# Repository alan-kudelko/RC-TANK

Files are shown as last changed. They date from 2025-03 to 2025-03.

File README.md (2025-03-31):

# Full-metal RC-TANK in 1:11 Scale
Project of full-metal RC-TANK in 1:11 scale made from 3mm thick steel sheets  
### 1. Requirements:

Tab.1.1 Tank Dimensions

| Dimension | |
|---|---|
| $Length$ | 70 [cm] |
| $Width_{1}$  | 32 [cm] |
| $Width_{2}$  | 42 [cm] |
| $Height$ | 20 [cm] |
| $Ground\ clearance$ | 5 [cm] |

###### $Width_{1}$ - Width of tank without tracks  
###### $Width_{2}$ - Width of tank with tracks  
2. Maximum speed  of at least $V_{Max}=5\frac{km}{h}$  
3. Input battery voltage $U_{In}=12.5V - 35V$  
4. DC Motors voltage $U_{m}=7.4V$  
### 2. Tracks and sprocket wheels

<picture>
 <source media="(prefers-color-scheme: dark)" srcset="Drivetrain/Tank_Tracks.png">
 <source media="(prefers-color-scheme: light)" srcset="Drivetrain/Tank_Tracks.png">
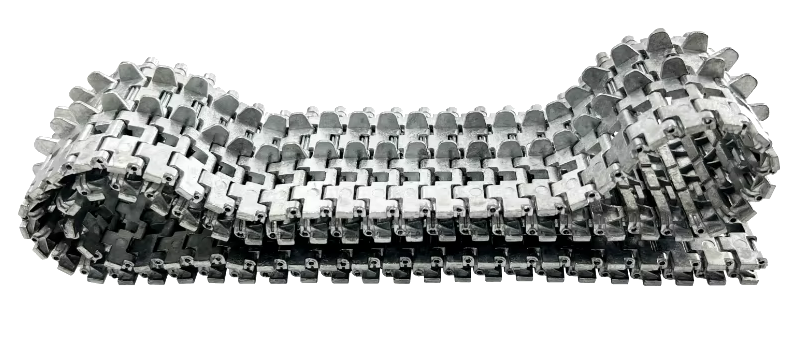
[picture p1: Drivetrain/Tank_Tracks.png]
 
</picture>

<picture>
 <source media="(prefers-color-scheme: dark)" srcset="Drivetrain/Sprocket_Wheel.png">
 <source media="(prefers-color-scheme: light)" srcset="Drivetrain/Sprocket_Wheel.png">
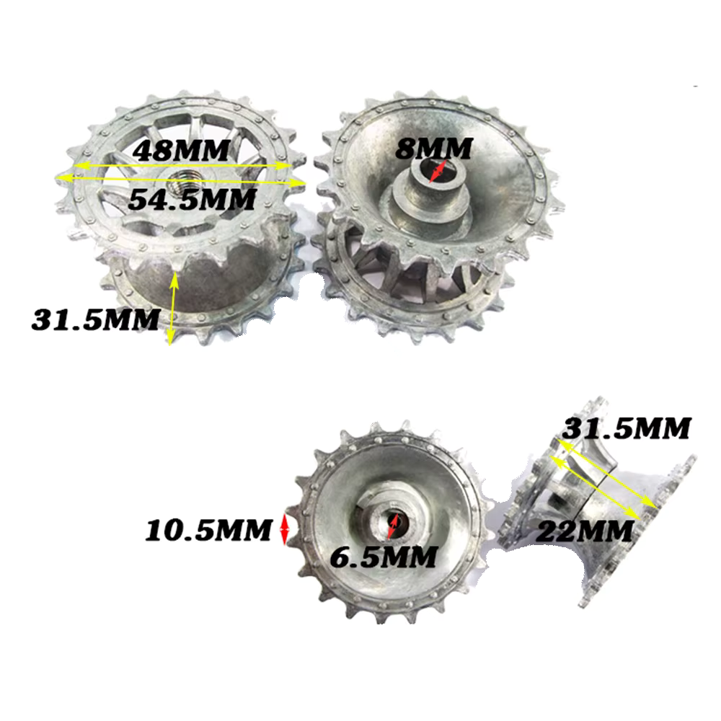
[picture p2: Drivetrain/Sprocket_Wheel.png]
 
</picture>

### 3. DC Motors selection
<picture>
 <source media="(prefers-color-scheme: dark)" srcset="Drivetrain/Injora540_13T_Parameters.png">
 <source media="(prefers-color-scheme: light)" srcset="Drivetrain/Injora540_13T_Parameters.png">
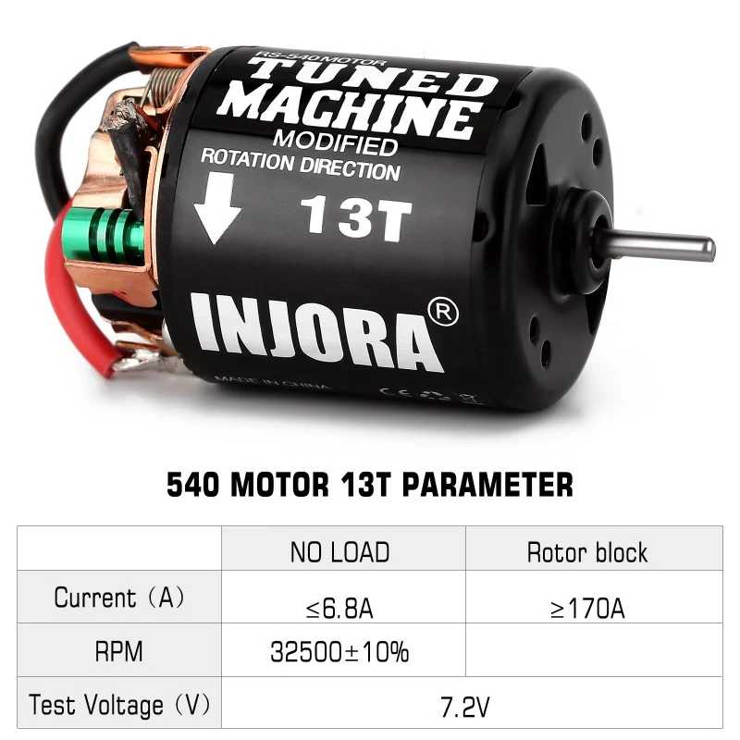
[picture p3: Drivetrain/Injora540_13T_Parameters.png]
 
</picture>

<picture>
 <source media="(prefers-color-scheme: dark)" srcset="Drivetrain/Injora540_Parameters_Comparison.png">
 <source media="(prefers-color-scheme: light)" srcset="Drivetrain/Injora540_Parameters_Comparison.png">
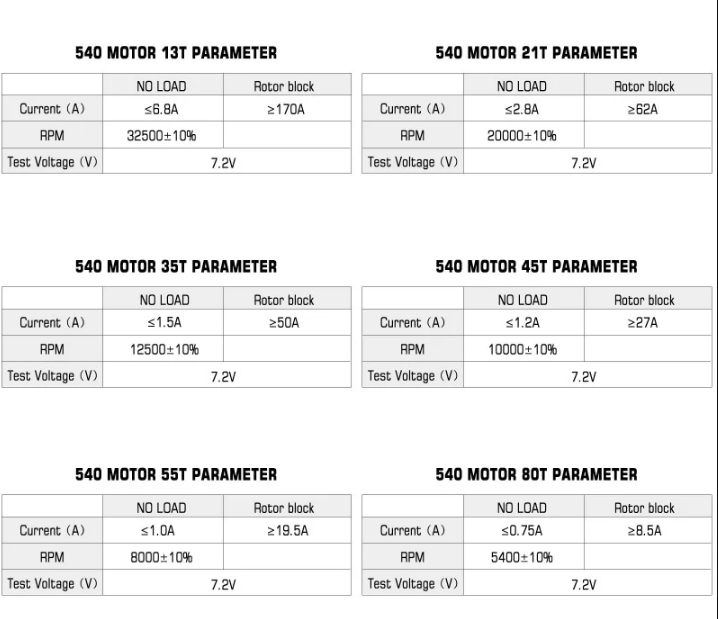
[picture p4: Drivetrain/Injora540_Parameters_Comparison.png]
 
</picture>

According to graphs Injora 540 13T has the highest peak power of around 300W but its RPM is too high for usage in a RC Tank. In order to able to move heavy vehicle we need to use a gearbox.

<picture>
 <source media="(prefers-color-scheme: dark)" srcset="Drivetrain/DC_Motor_Selection.png">
 <source media="(prefers-color-scheme: light)" srcset="Drivetrain/DC_Motor_Selection.png">
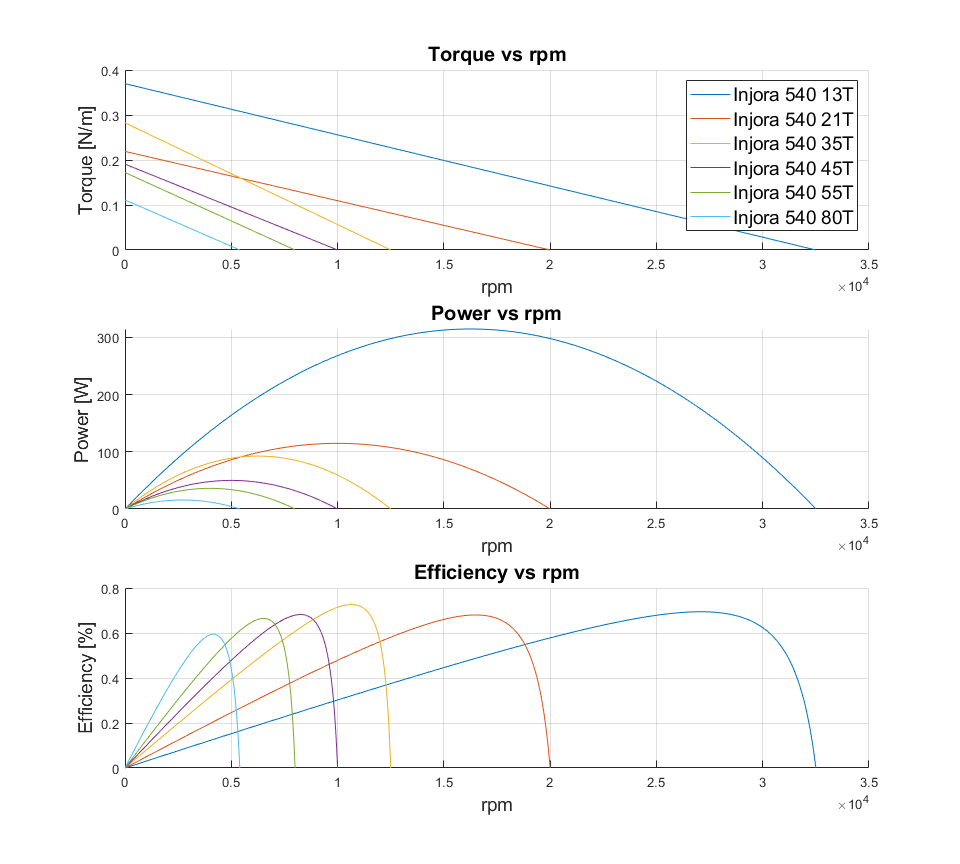
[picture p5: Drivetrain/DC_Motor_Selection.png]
 
</picture>

### 4. Gearbox selection   
<picture>
 <source media="(prefers-color-scheme: dark)" srcset="Drivetrain/DC_Motor_Gearbox_1_50.png">
 <source media="(prefers-color-scheme: light)" srcset="Drivetrain/DC_Motor_Gearbox_1_50.png">
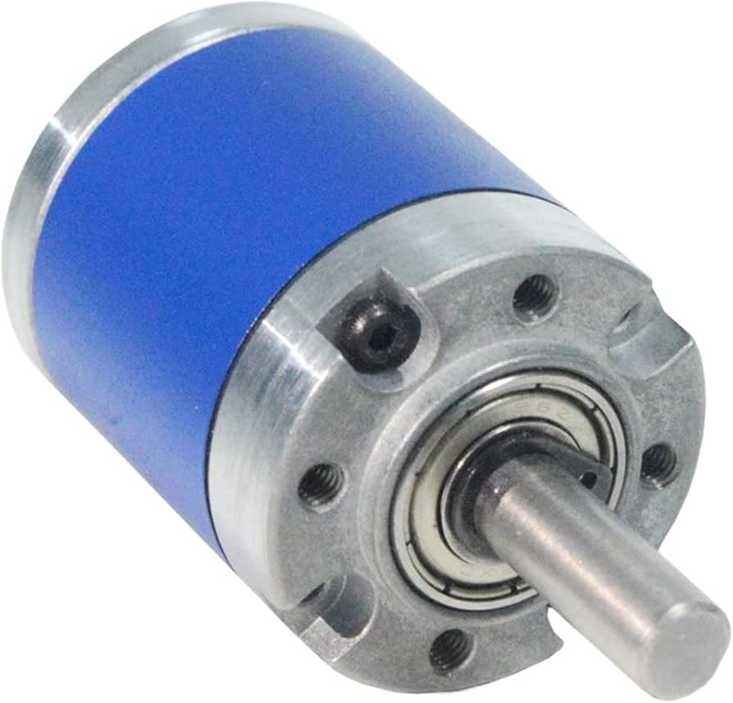
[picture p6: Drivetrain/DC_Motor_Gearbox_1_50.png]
 
</picture>

<picture>
 <source media="(prefers-color-scheme: dark)" srcset="Drivetrain/DC_Motor_Gearbox_dims_1.png">
 <source media="(prefers-color-scheme: light)" srcset="Drivetrain/DC_Motor_Gearbox_dims_1.png">
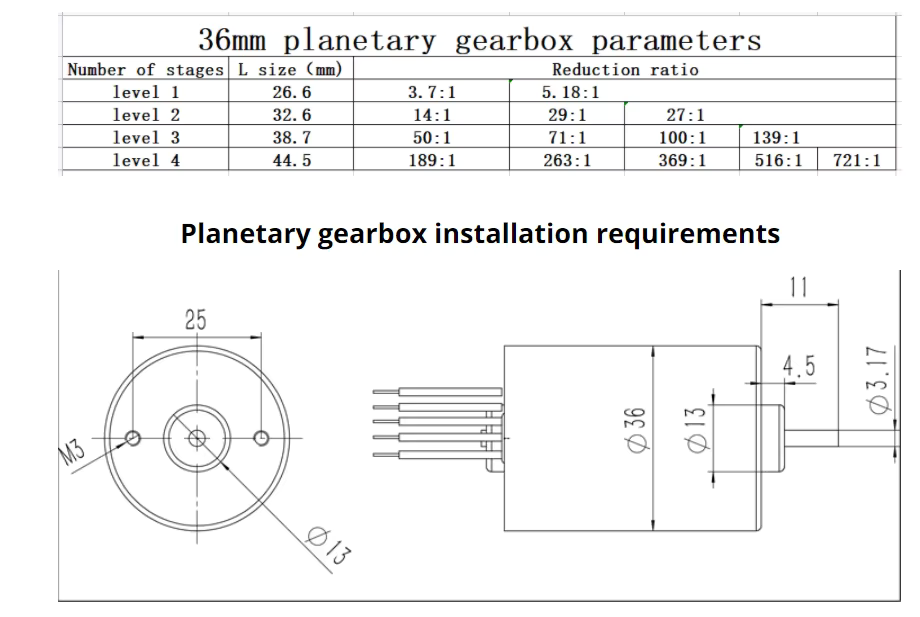
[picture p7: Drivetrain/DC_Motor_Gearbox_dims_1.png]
 
</picture>

<picture>
 <source media="(prefers-color-scheme: dark)" srcset="Drivetrain/DC_Motor_Gearbox_dims_2.png">
 <source media="(prefers-color-scheme: light)" srcset="Drivetrain/DC_Motor_Gearbox_dims_2.png">
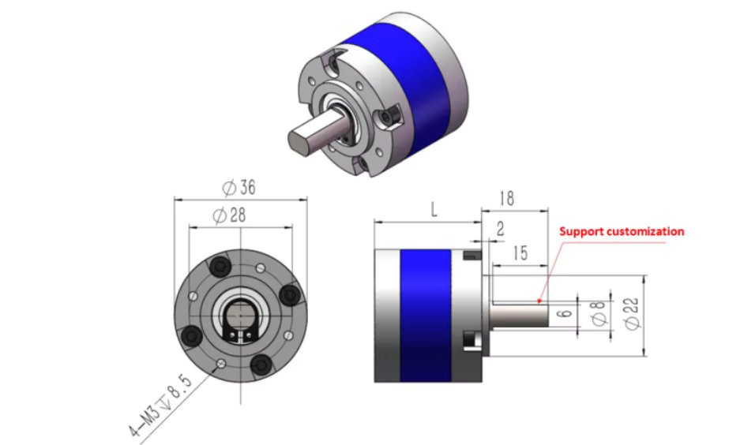
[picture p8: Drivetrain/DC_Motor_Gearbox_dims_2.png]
 
</picture>

<picture>
 <source media="(prefers-color-scheme: dark)" srcset="Drivetrain/DC_Motor_Gearbox_Selection.png">
 <source media="(prefers-color-scheme: light)" srcset="Drivetrain/DC_Motor_Gearbox_Selection.png">
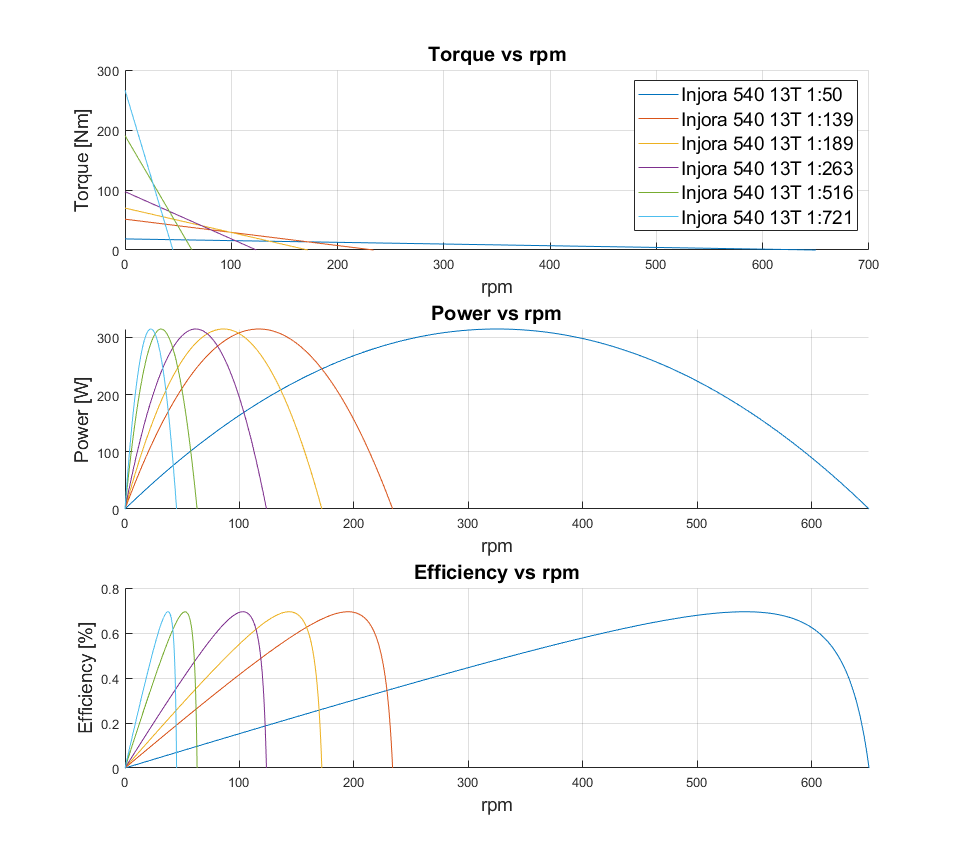
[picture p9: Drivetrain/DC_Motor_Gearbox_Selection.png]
 
</picture>

Speed of the tank has to be at least $V_{Max}=5\frac{km}{h}$

Tab.4.1 Drivetrain parameters

| Drivetrain parameters | |
|---|---|
| Sprocket wheel diameter | D=48 [mm] |
| RPM  | n=32500 [rpm] |
| Gearbox reduction  | r=1:50 |

We can see that the selected DC motor with 1:50 gearbox gives theoretical 650 rpm.

Using a formula 1) we can calculate maximum theoretical speed of a tank.

1) $V_{Max}=\pi\frac{D*rpm}{60}=1.63\frac{m}{s}=5.88\frac{km}{h} $

### 5. Switch mode power supply design
Switch mode power supply should be able to generate all the necessery voltages for use in the tank. That are 7.4V for DC motor, 5V for controll logic, 6V for servomechanisms and 12V for additional devices such as DC fans. Additionally it should feature a wide range of input voltages for instance 12.5V - 35V. On top of that power supply should have shortcircuit protection, undervoltage protection and overtemperature protection. Moreover, in order order to limit inrush current for the circuit I decided to use high-side mosfet as softstart.

Tab.5.1 Voltages and current requirements

| Voltage | Maximum current | Maximum power|
|---|---|---|
| 7.4 [V] | 40 [A] | 296 [W] |
| 12 [V] | 20 [A] | 240 [W] |
| 6 [V] | 20 [A] | 120 [W] |
| 5 [V] | 5 [A]  | 25 [W]  |
| Total | 85 [A] | 681 [W] |

When designing switch mode power supply it is advised to choose the right topology depending on power output. That's why, I have decided to use half-bridge topology for sections 7.4V and 12V and buck topology for sections 5V and 6V.

Tab.5.2 Design requirements for section 7.4V

| Voltage | Maximum power|
|---|---|
| Topology| Half-Bridge |
| Output voltage | 7.4 [V]|
| Output current | 40 [A]|
| Working frequency | 500 [kHz] |
| Coil inductance min. | 16 [uH] |
| Coil core material | T130-52 |
| Coil wire diameter | 2.36 [mm] |
| Switching transistors | IXTH94N20X4 |
| Conduction and switching losses per transistor | 22.5 [W] |
| Total power losses| 45 [W]|
| PWM Controller | TL3843 |
| Mosfet driver | IRS2008 |

Tab.5.3 Design requirements for section 12V

| Voltage | Maximum power|
|---|---|
| Topology| Half-Bridge |
| Output voltage | 12 [V]|
| Output current | 20 [A]|
| Working frequency | 500 [kHz] |
| Coil inductance min. | 16 [uH] |
| Coil core material | T106-26B |
| Coil wire diameter | 1.60 [mm] |
| Switching transistors | STP60NF06 |
| Conduction and switching losses per transistor | 16.6 [W]|
| Total power losses | 33.2 [W]|
| PWM Controller | TL3843 |
| Mosfet driver | IRS2008 |

Tab.5.4 Design requirements for section 6V

| Voltage | Maximum power|
|---|---|
| Topology| Buck |
| Output voltage | 6.0 [V]|
| Output current | 20 [A]|
| Working frequency | 500 [kHz] |
| Coil inductance min. | 16 [uH] |
| Coil core material | T106-26B |
| Coil wire diameter | 1.60 [mm] |
| Switching transistor | STP60NF06 |
| Freewheeling diode| RHRP3060|
| Conduction and switching losses in transistors | 16.6 [W] |
| Conduction losses in freewheeling diode| 14 [W]|
| Total power losses | 30.6 [W]|
| PWM Controller | TL3843 |
| Mosfet driver | IRS20752 |

Tab.5.5 Design requirements for section 5V

| Voltage | Maximum power|
|---|---|
| Topology| Buck |
| Output voltage | 5 [V]|
| Output current | 5 [A]|
| Working frequency | 500 [kHz] |
| Coil inductance min. | 16 [uH] |
| Coil core material | T72-52 |
| Coil wire diameter | 0.80 [mm] |
| Switching transistor | STP60NF06 |
| Freewheeling diode| SB560 |
| Conduction and switching losses in transistors | 2.95 [W] |
| Conduction losses in freewheeling diode| 2.8 [W]|
| Total power losses | 5.75 [W]|
| PWM Controller | TL3843 |
| Mosfet driver | IRS20752 |

Tab.5.6 Design requirements for input section

| Voltage | Maximum power|
|---|---|
| Input voltage | 12.5 - 35 [V]|
| Input current | 85 [A]|
| Softstart transistor | IRF100P218AKMA1 |
| Conduction and switching losses in transistors | 9.25 [W] |

Mosfet power losses were calculated using online calculator https://www.heatsinkcalculator.com/mosfet-power-loss-calculator.html   
Gate charge losses were negligible that is why they are not included

Overall simplified schematic of whole SMPS will look similiar to that:

<picture>
 <source media="(prefers-color-scheme: dark)" srcset="SMPS/SMPS_Simplified.PNG">
 <source media="(prefers-color-scheme: light)" srcset="SMPS/SMPS_Simplified.PNG">
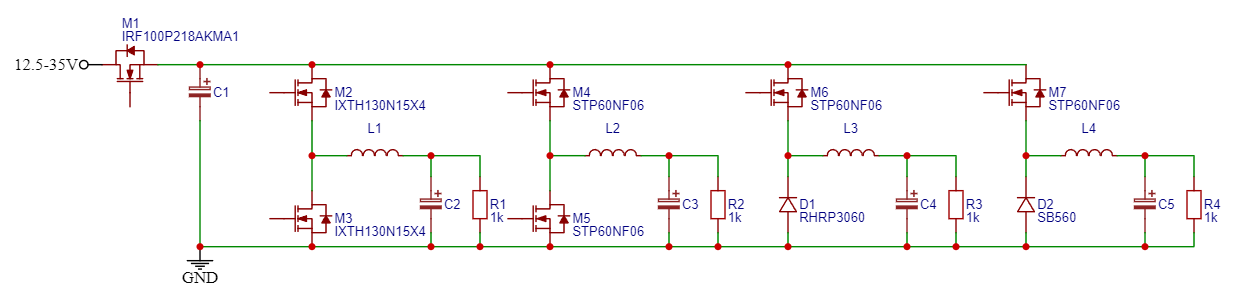
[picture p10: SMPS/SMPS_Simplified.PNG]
 
</picture>

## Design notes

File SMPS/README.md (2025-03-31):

# Switch mode power supply for RC-TANK
Switch mode power supply should be able to generate all the necessery voltages for use in the tank. That are 7.4V for DC motor, 5V for controll logic, 6V for servomechanisms and 12V for additional devices such as DC fans. Additionally it should feature a wide range of input voltages for instance 12.5V - 35V. On top of that power supply should have shortcircuit protection, undervoltage protection and overtemperature protection. Moreover, in order order to limit inrush current for the circuit I decided to use high-side mosfet as softstart.

Tab.1.1 Voltages and current requirements

| Voltage | Maximum current | Maximum power|
|---|---|---|
| 7.4 [V] | 40 [A] | 296 [W] |
| 12 [V] | 20 [A] | 240 [W] |
| 6 [V] | 20 [A] | 120 [W] |
| 5 [V] | 5 [A]  | 25 [W]  |
| Total | 85 [A] | 681 [W] |

When designing switch mode power supply it is advised to choose the right topology depending on power output. That's why, I have decided to use half-bridge topology for sections 7.4V and 12V and buck topology for sections 5V and 6V.

Tab.1.2 Design requirements for section 7.4V

| Voltage | Maximum power|
|---|---|
| Topology| Half-Bridge |
| Output voltage | 7.4 [V]|
| Output current | 40 [A]|
| Working frequency | 500 [kHz] |
| Coil inductance min. | 16 [uH] |
| Coil core material | T130-52 |
| Coil wire diameter | 2.36 [mm] |
| Switching transistors | IXTH94N20X4 |
| Conduction and switching losses per transistor | 22.5 [W] |
| Total power losses| 45 [W]|
| PWM Controller | TL3843 |
| Mosfet driver | IRS2008 |

Tab.1.3 Design requirements for section 12V

| Voltage | Maximum power|
|---|---|
| Topology| Half-Bridge |
| Output voltage | 12 [V]|
| Output current | 20 [A]|
| Working frequency | 500 [kHz] |
| Coil inductance min. | 16 [uH] |
| Coil core material | T106-26B |
| Coil wire diameter | 1.60 [mm] |
| Switching transistors | STP60NF06 |
| Conduction and switching losses per transistor | 16.6 [W]|
| Total power losses | 33.2 [W]|
| PWM Controller | TL3843 |
| Mosfet driver | IRS2008 |

Tab.1.4 Design requirements for section 6V

| Voltage | Maximum power|
|---|---|
| Topology| Buck |
| Output voltage | 6.0 [V]|
| Output current | 20 [A]|
| Working frequency | 500 [kHz] |
| Coil inductance min. | 16 [uH] |
| Coil core material | T106-26B |
| Coil wire diameter | 1.60 [mm] |
| Switching transistor | STP60NF06 |
| Freewheeling diode| RHRP3060|
| Conduction and switching losses in transistors | 16.6 [W] |
| Conduction losses in freewheeling diode| 14 [W]|
| Total power losses | 30.6 [W]|
| PWM Controller | TL3843 |
| Mosfet driver | IRS20752 |

Tab.1.5 Design requirements for section 5V

| Voltage | Maximum power|
|---|---|
| Topology| Buck |
| Output voltage | 5 [V]|
| Output current | 5 [A]|
| Working frequency | 500 [kHz] |
| Coil inductance min. | 16 [uH] |
| Coil core material | T72-52 |
| Coil wire diameter | 0.80 [mm] |
| Switching transistor | STP60NF06 |
| Freewheeling diode| SB560 |
| Conduction and switching losses in transistors | 2.95 [W] |
| Conduction losses in freewheeling diode| 2.8 [W]|
| Total power losses | 5.75 [W]|
| PWM Controller | TL3843 |
| Mosfet driver | IRS20752 |

Tab.1.6 Design requirements for input section

| Voltage | Maximum power|
|---|---|
| Input voltage | 12.5 - 35 [V]|
| Input current | 85 [A]|
| Softstart transistor | IRF100P218AKMA1 |
| Conduction and switching losses in transistors | 9.25 [W] |

Mosfet power losses were calculated using online calculator https://www.heatsinkcalculator.com/mosfet-power-loss-calculator.html   
Gate charge losses were negligible that is why they are not included

Overall simplified schematic of whole SMPS will look similiar to that:

<picture>
 <source media="(prefers-color-scheme: dark)" srcset="SMPS_Simplified.PNG">
 <source media="(prefers-color-scheme: light)" srcset="SMPS_Simplified.PNG">
 YOUR-ALT-TEXT
</picture>

Current project of PCB board is a proof of concept which will allow to test the following:
1. Input MOSFET with RC circuit softstart   
2. TL3843 - PWM Controller   
3. IRS20752 - High side MOSFET DRIVER with bootstraping   
4. Output voltages   
5. Step-up conveter for gate of input MOSFET

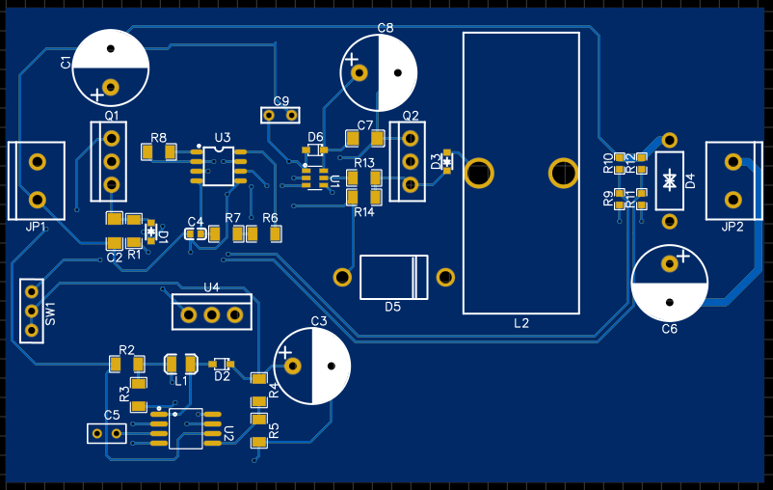
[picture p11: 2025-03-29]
SMPS/RCTank2025_SMPS_V1/RCTank2025_SMPS_V1_Front_2D.PNG

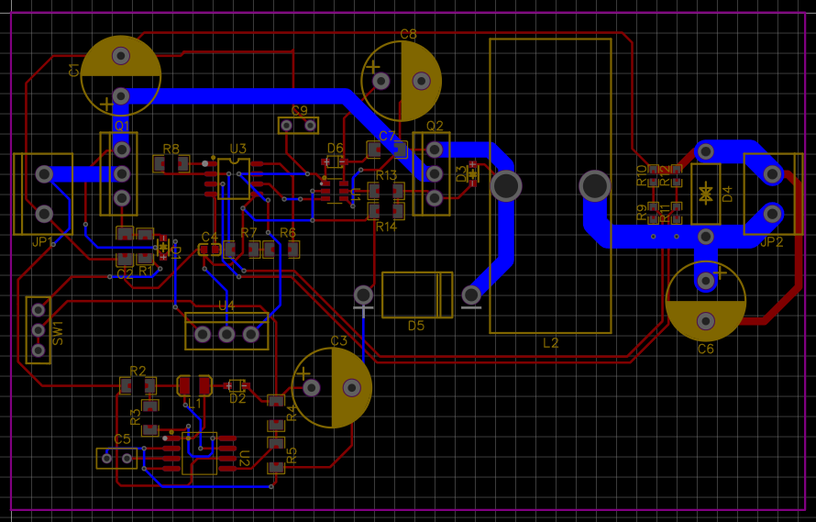
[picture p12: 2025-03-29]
SMPS/RCTank2025_SMPS_V1/RCTank2025_SMPS_V1_Back_Copper.PNG

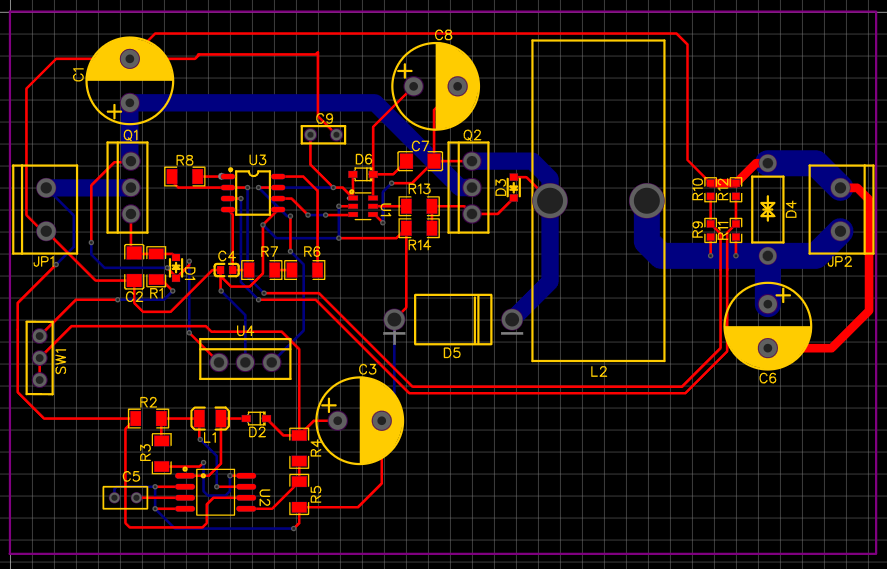
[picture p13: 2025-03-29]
SMPS/RCTank2025_SMPS_V1/RCTank2025_SMPS_V1_Front_Copper.PNG

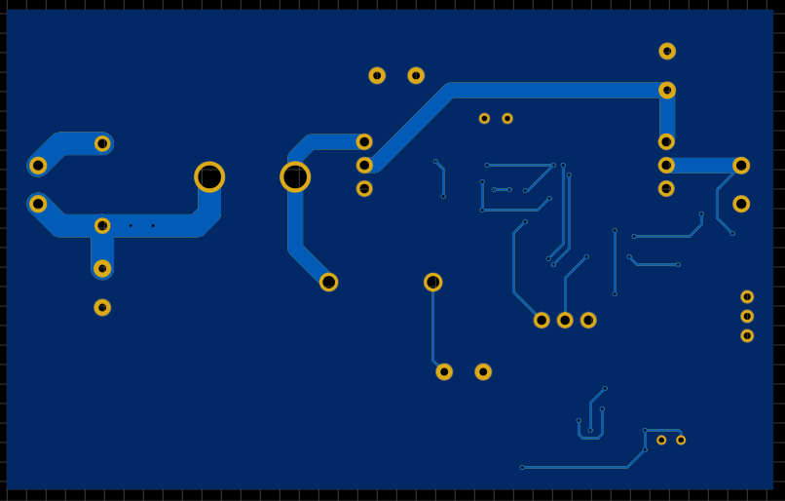
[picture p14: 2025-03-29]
SMPS/RCTank2025_SMPS_V1/RCTank2025_SMPS_V1_Back_2D.PNG

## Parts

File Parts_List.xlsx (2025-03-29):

Price [zł] | Price [zł/pcs] | PCS | Part | Link
582.12 zł | 145.53 zł | 4 | Heng Long All Metal Track 1/16 RC Germany Tiger | https://www.henglong1986.com/product/heng-long-all-metal-track-for-robot-tank3818-116-1-16-rc-germany-tiger-1-pcs-diy/
40.60 zł | 20.3 | 2 | Black Steel sheet 70mm x 10mm x 3mm
85.12 zł | 42.56 | 2 | INJORA 540 13T Brushed Motor | https://www.injora.com/products/540-brushed-motor-35t-45t-55t-for-1-10-rc-crawler?variant=39726127972400
220.00 zł | 55 | 4 | Heng long Sprocket wheel 1/16 RC Germany Tiger
149.60 zł | 74.8 | 2 | Planetary gearbox for 540 Brushed Motor
0.00 zł
0.00 zł
0.00 zł

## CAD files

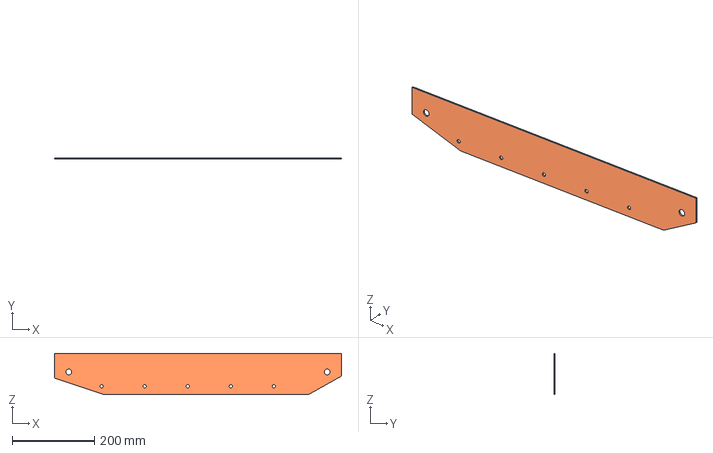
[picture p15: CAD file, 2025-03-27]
Chassis/Chassis_Side.FCStd
700.0 x 3.00 x 100.0 mm

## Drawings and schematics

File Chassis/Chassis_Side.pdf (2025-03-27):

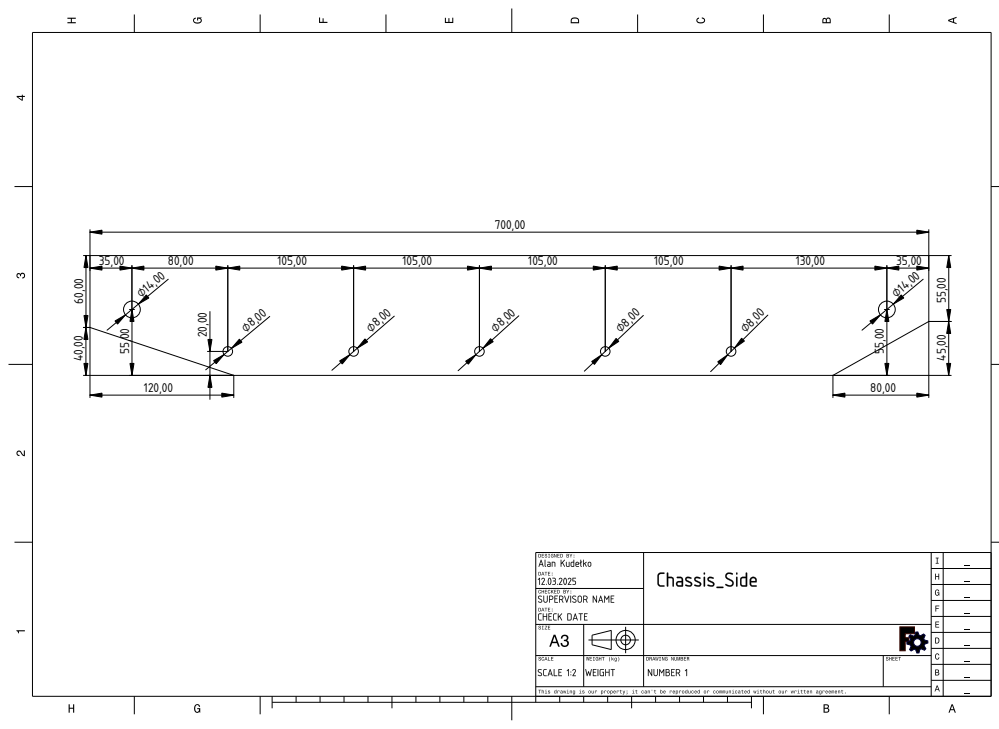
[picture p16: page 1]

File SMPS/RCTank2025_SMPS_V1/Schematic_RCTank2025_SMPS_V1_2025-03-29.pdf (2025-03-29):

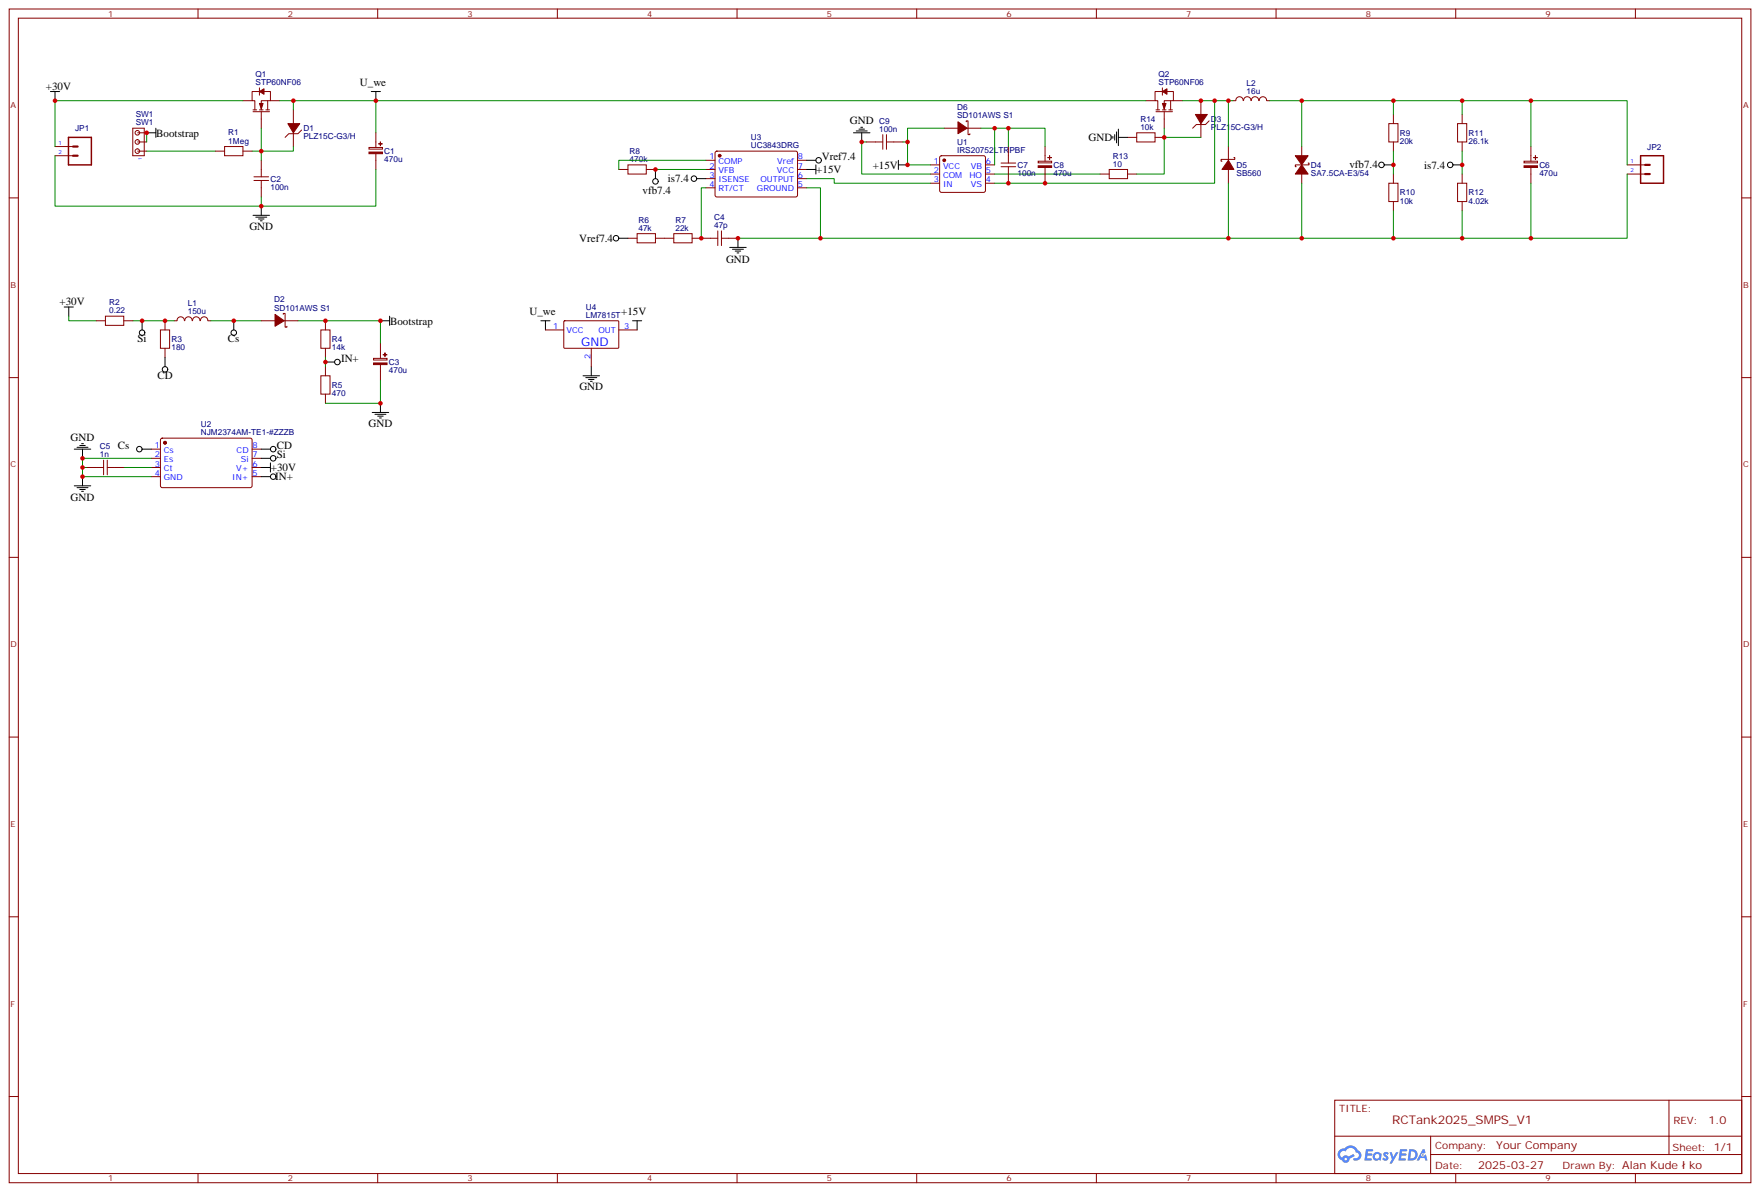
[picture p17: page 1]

Drawn By: Alan Kude ko

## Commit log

2025-03-26 Chassis drawing
    [WannaV2.FCStd]
2025-03-27 Chassis side project
    [Chassis_Side.FCStd, WannaV2.FCStd]
2025-03-28 Part list update
    [Parts_List.xlsx]
2025-03-28 Parts update
    [Parts_List.xlsx]
2025-03-28 Drivetrain dc motor selection
2025-03-29 Drivetrain update
    [Parts_List.xlsx]
2025-03-29 Tracks and sprocket wheels
2025-03-29 Gearbox dimensions
2025-03-29 Part list and DC Motor
    [Parts_List.xlsx]
2025-03-31 Drivetrain parts slection
2025-03-31 SMPS simplified schematic
2025-04-17 Add files via upload
    Live view of PCB
